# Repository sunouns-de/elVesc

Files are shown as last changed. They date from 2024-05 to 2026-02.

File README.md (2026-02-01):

# README

`Status: Completed (Archive State).`

This project is no longer being maintained as an active WIP. The primary reason is the availability of official VESC peripherals (such as the [VESC Dash 35B](https://www.vesclabs.com/product/vesc-dash-35b/) or the [VESC Rmcore](https://www.vesclabs.com/product/vesc-rmcore/)), which cover many of the original goals (CAN connectivity, LispBM scripting) natively and, in some aspects, more effectively.

**Important notes on the current state:**
1. **PCB Design:** The latest PCB design in this repository still contains errors. The board layout needs to be cross-checked against the schematics and revised before it can be considered fully functional.
2. **12V High-Side Switching:** Unlike many other solutions, including official ones like the RmCore, this design explicitly supports 12V high-side switching for vehicle lighting.
3. **Hardware Fixes:** The horn circuitry has already been corrected in the schematic but has not yet been implemented in the physical PCB layout.

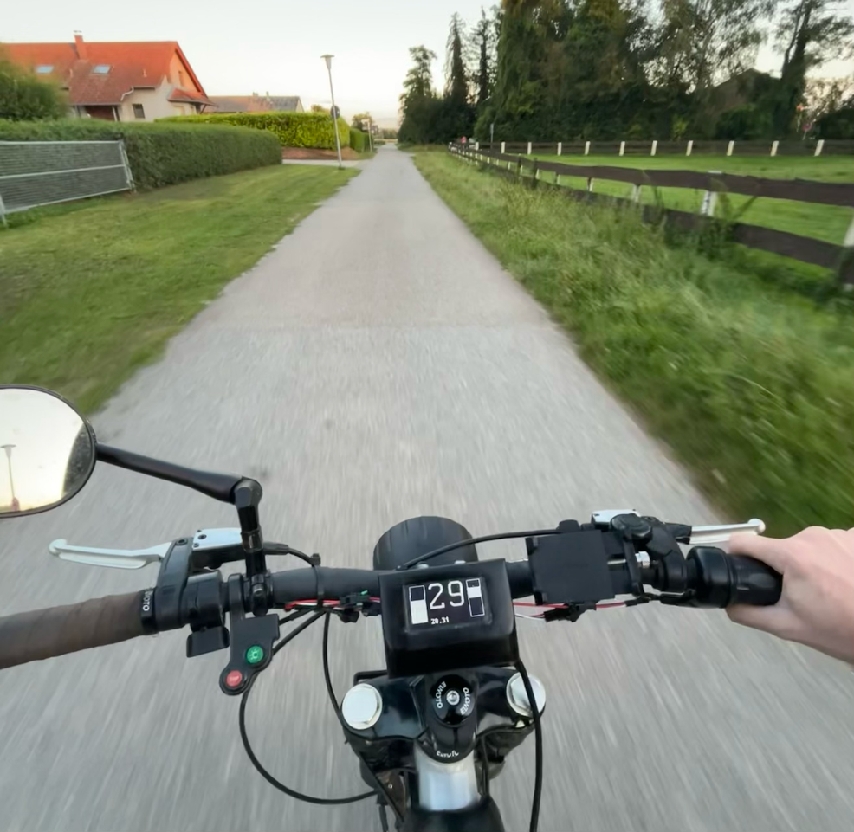
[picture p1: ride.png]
Summer 2024


## Overview

You find the code, flashable on an ESP32 DevKitC with PlatformIO in the submodule.

Everything needed for the PCB inside pcb-schematics.

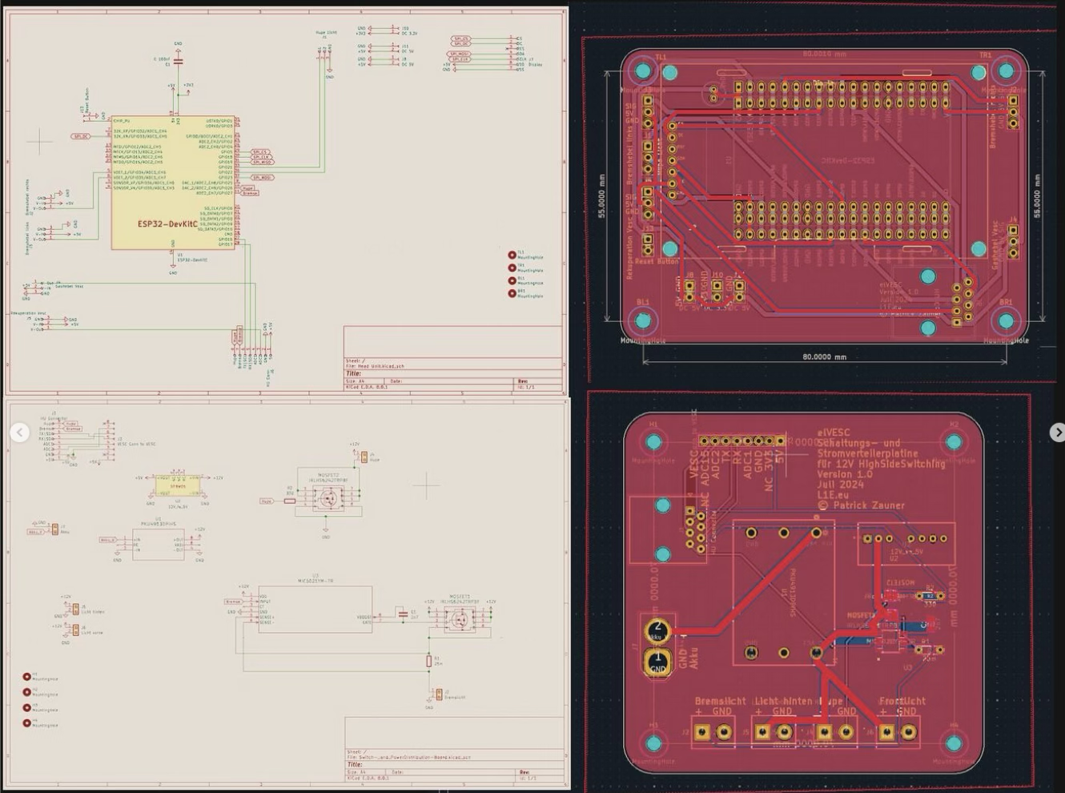
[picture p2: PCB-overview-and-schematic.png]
pcb-schematics


Link to Onshape Design of Headunit Mount in directory 3d design.
Other project designs will also be added here.

## Core concept

Replacement for original board electronics and an open platform to have a tachometer for any [VESC](https://vesc-project.com/) powered E-Bike.

### Headunit (Display)

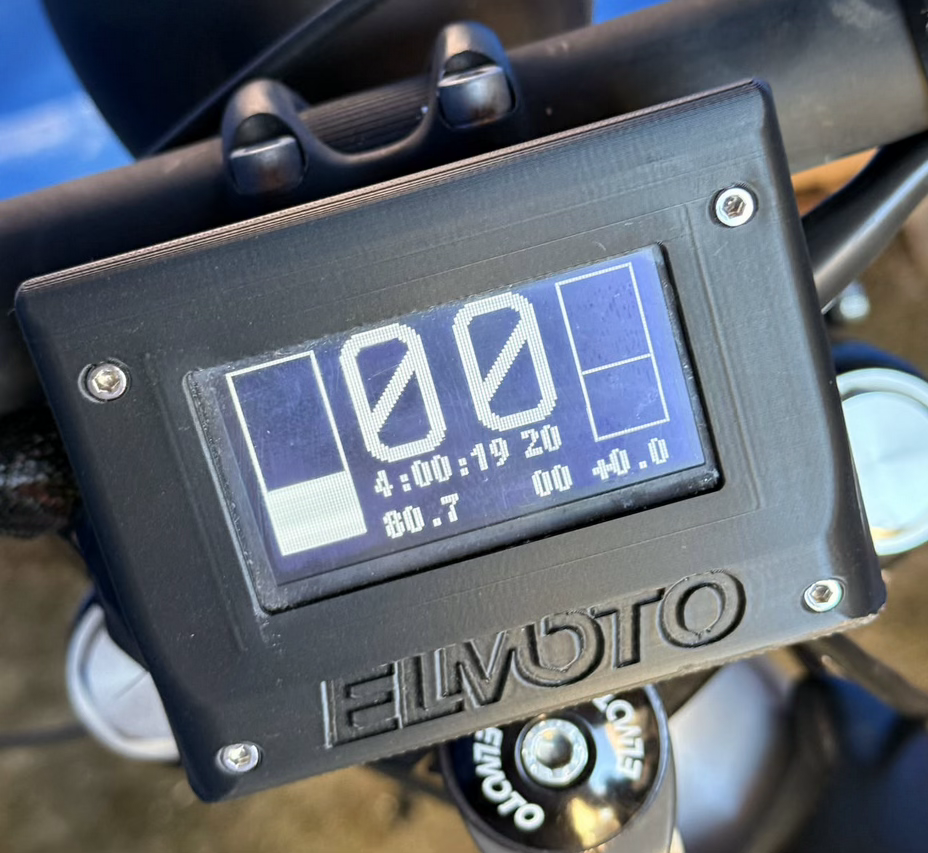
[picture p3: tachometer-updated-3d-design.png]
Tachometer in current housing


#### Implemented and working
Currently working on Tachometer:
- Speed
- Trip Kilometer (resets every power cycle)
- Time since Startup
- Average Speed
- Battery Voltage (mapped to left bar)
- Motor Current (mapped to right bar)
- Motor Power in kW (below right bar)
- Brake Lights
 - triggered when pulling any brake lever
 - also triggered when using regenerative braking above a configurable motor current

Currently all values (wheel diameter, battery voltage, max current, etc.) are hard coded.

Proper way for multiple bikes will be to utilize config files.

#### Implemented but not working
- Average Wh per km consumption
- Horn (probably hardware issue due to bad soldering)

#### Planned
- Odometer (saving distance to ESP32 flash)
- Don't try to calculate values like average speed or  but just get them from VESC

##### Ideas
- Smaller headunit but with more features: Utilizing also an ESP 32 C6 with Zigbee
 - Home Assistant integration
- OTA Updates
- Blinkers but requires more Pins on ESP32 or multiplexing
  - Also requires more than current 8 wires by using a normal RJ45-connector and Ethernet-cable to bottom or serial communication and therefore another microcontroller on the SPDB.

### Switching and Power Distribution Board (SPDB)

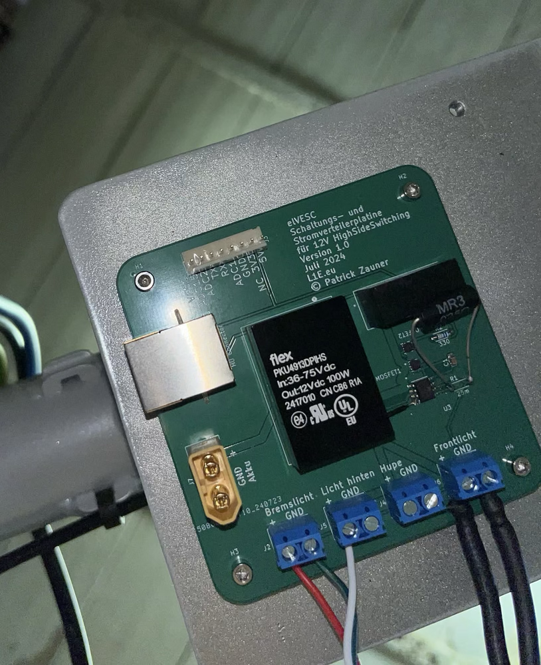
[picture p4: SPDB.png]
Switching and Power Distribution


Converts high battery voltage to 12V for the headlights and other components. (DC
/DC converter is not cheap, but great quality and has pleanty of headroom)

Also provides 5V for the Headunit: ESP32, Hall-Effect-Brake-Levers and Display. (ESP32 runs on 3V but the dev kit converts the incoming 5V to the usable 3V)

Connects the VESC to the rest of the system.

Turns on Brakelights and also provides power for the 12V lights.

#### Planned
- components with bigger footprints for easier soldering
 - MOSFETs
 - capacitors
 - resistors

#### Ideas

- USB-C in port and DC/DC converter for charging big E-Bike battery (not _really_ practical but I really want this hehe)
- USB-C out port for charging other devices or at least another 12V out to use existing products for this
- Eventually blinkers (my L1E-class-bike came without them from the manufacturer so they are not mandatory)

In combination with Headunit: Serial connection / CAN-BUS based system.

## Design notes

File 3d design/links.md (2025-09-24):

[Display Mount (Govecs has rights of logo)](https://cad.onshape.com/documents/d2e54b8ad2f1a2405cf1981f/w/7cc03ec50020e00fa81f538a/e/62ff2c873d72c78bf2272509)

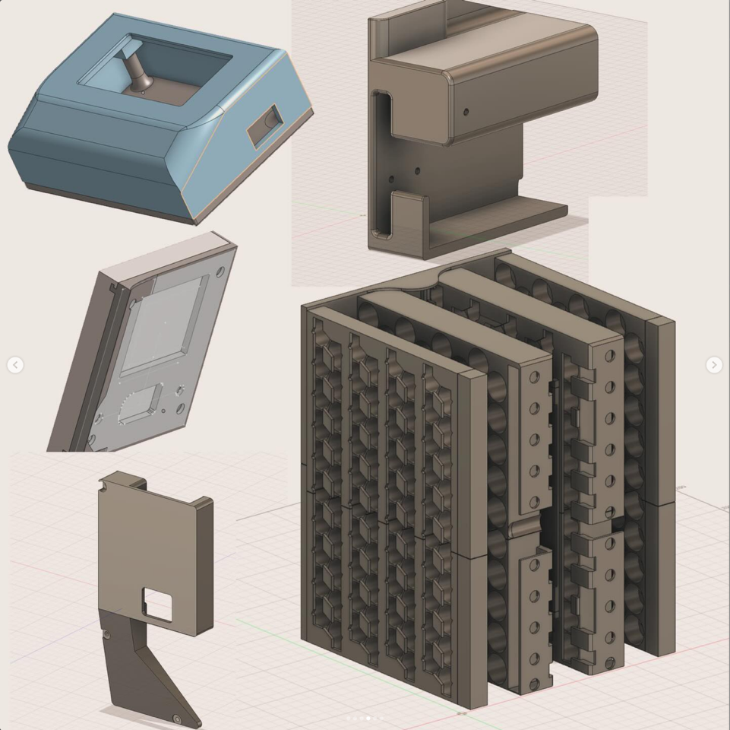
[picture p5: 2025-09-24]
3d-models-overview.png

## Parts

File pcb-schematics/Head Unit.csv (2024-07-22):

Id | Designator | Footprint | Quantity | Designation | Supplier and ref
1 | J10 | PinHeader_1x02_P2.54mm_Vertical | 1 | DC 3.3V
2 | J5 | PinHeader_1x03_P2.54mm_Vertical | 1 | Rekuperation Vesc
3 | J4 | PinHeader_1x03_P2.54mm_Vertical | 1 | Gashebel Vesc
4 | J7 | DIYMORE.CC | 1 | Display
5 | J8,J11 | PinHeader_1x02_P2.54mm_Vertical | 2 | DC 5V
6 | J3 | PinHeader_1x03_P2.54mm_Vertical | 1 | Bremshebel links
7 | J1 | PinHeader_1x03_P2.54mm_Vertical | 1 | Hupe Licht
8 | J2 | PinHeader_1x03_P2.54mm_Vertical | 1 | Bremshebel rechts
9 | J13 | PinHeader_1x02_P2.54mm_Vertical | 1 | Reset Button
10 | J6 | RJ45_Amphenol_54602-x08_Horizontal | 1 | HU Conn
11 | C1 | C_Radial_D5.0mm_H5.0mm_P2.00mm | 1 | C 100nF
12 | U1 | ESP32-DevKitC | 1 | ESP32-DevKitC

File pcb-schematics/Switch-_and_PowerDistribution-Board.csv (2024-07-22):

Id | Designator | Footprint | Quantity | Designation | Supplier and ref
1 | U2 | DPBW06_MWU | 1 | 12V_to_5V
2 | J2 | TerminalBlock_bornier-2_P5.08mm | 1 | Bremslicht
3 | R2 | R_Axial_DIN0204_L3.6mm_D1.6mm_P5.08mm_Horizontal | 1 | 330
4 | J3 | PinHeader_1x08_P2.54mm_Vertical | 1 | VESC Conn to VESC
5 | U1 | PKU4913DPIHS_FPM | 1 | PKU4913DPIHS
6 | J6 | TerminalBlock_bornier-2_P5.08mm | 1 | Licht vorne
7 | C1 | C_Radial_D5.0mm_H5.0mm_P2.00mm | 1 | 2n7
8 | J1 | RJ45_Amphenol_54602-x08_Horizontal | 1 | HU Connector
9 | MOSFET1,MOSFET2 | PQFN6_2X2_INF | 2 | IRLHS6242TRPBF
10 | J7 | AMASS_XT60-F_1x02_P7.20mm_Vertical | 1 | Akku
11 | R1 | R_Axial_DIN0204_L3.6mm_D1.6mm_P5.08mm_Horizontal | 1 | 25m
12 | U3 | SOIC-8_M_MCH | 1 | MIC5021YM-TR
13 | J5 | TerminalBlock_bornier-2_P5.08mm | 1 | Licht hinten
14 | J4 | TerminalBlock_bornier-2_P5.08mm | 1 | Hupe

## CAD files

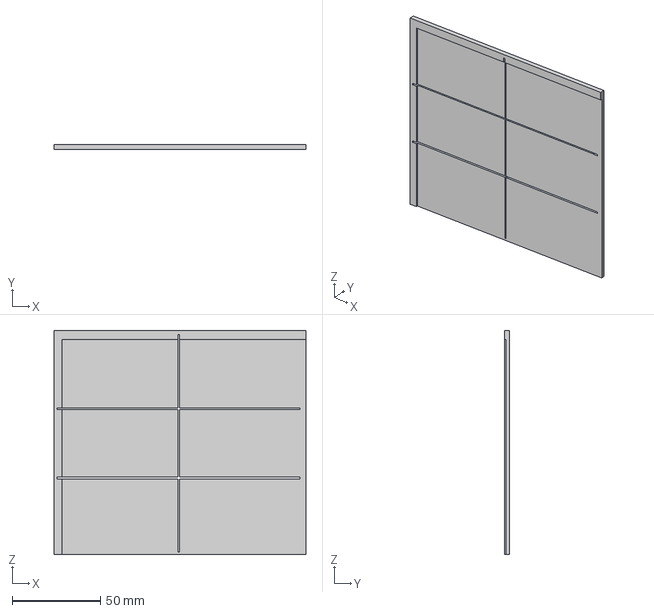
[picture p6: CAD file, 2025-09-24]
3d design/Schablone.3mf
142.7 x 3.00 x 126.9 mm

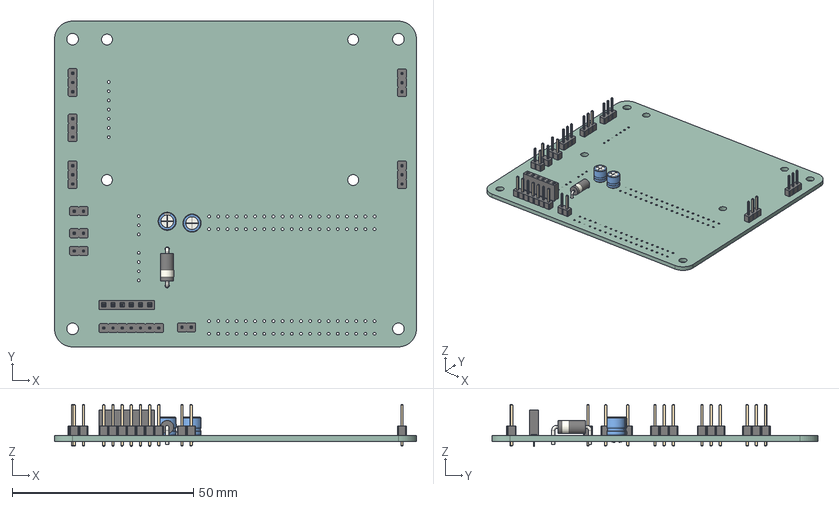
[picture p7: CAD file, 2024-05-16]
pcb-schematics/Head Unit/Head Unit.step
100.0 x 90.0 x 11.6 mm
CP_Radial_D50mm_P200mm
PinHeader_1x02_P254mm_Vertical x 4
C_Radial_D50mm_H50mm_P200mm
PinHeader_1x03_P254mm_Vertical x 5
D_DO-15_P10.16mm_Horizontal
PinHeader_1x07_P254mm_Vertical
PinSocket_1x06_P254mm_Vertical
Head Unit_PCB

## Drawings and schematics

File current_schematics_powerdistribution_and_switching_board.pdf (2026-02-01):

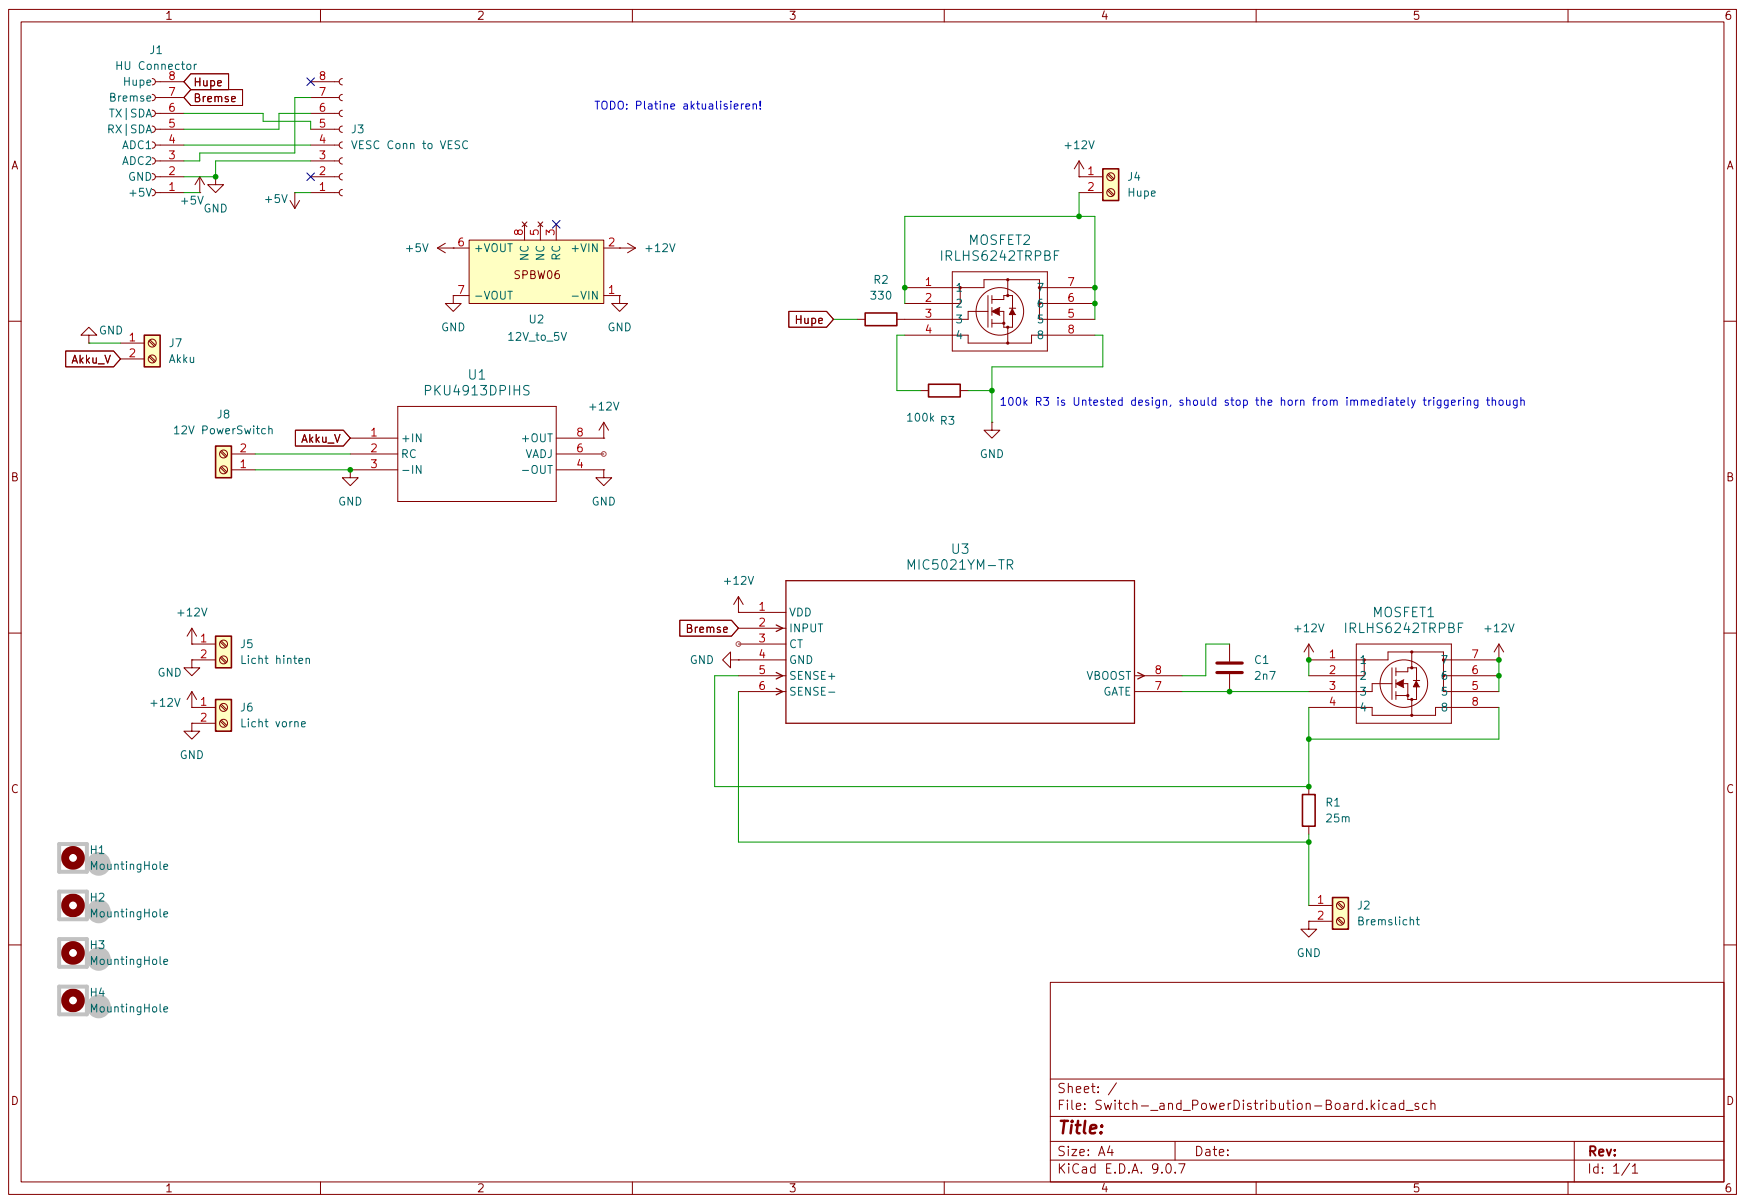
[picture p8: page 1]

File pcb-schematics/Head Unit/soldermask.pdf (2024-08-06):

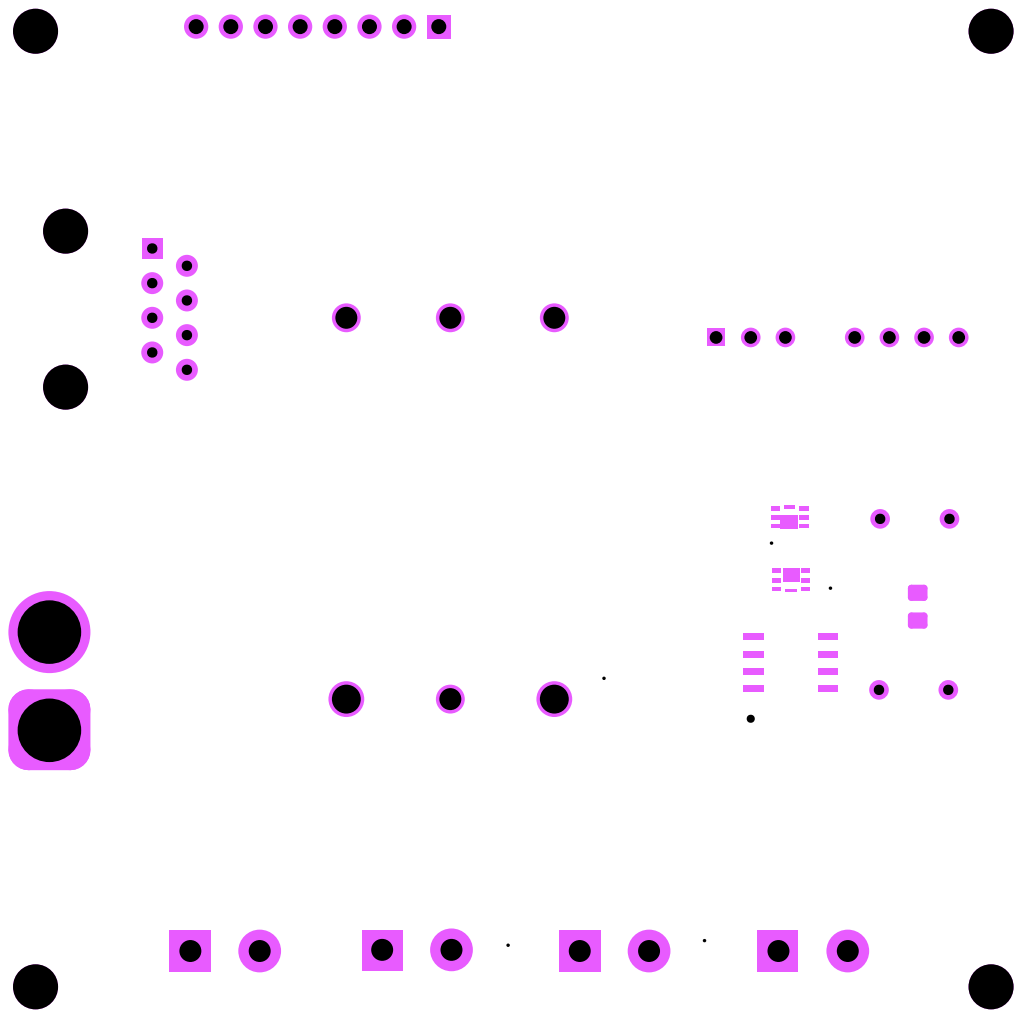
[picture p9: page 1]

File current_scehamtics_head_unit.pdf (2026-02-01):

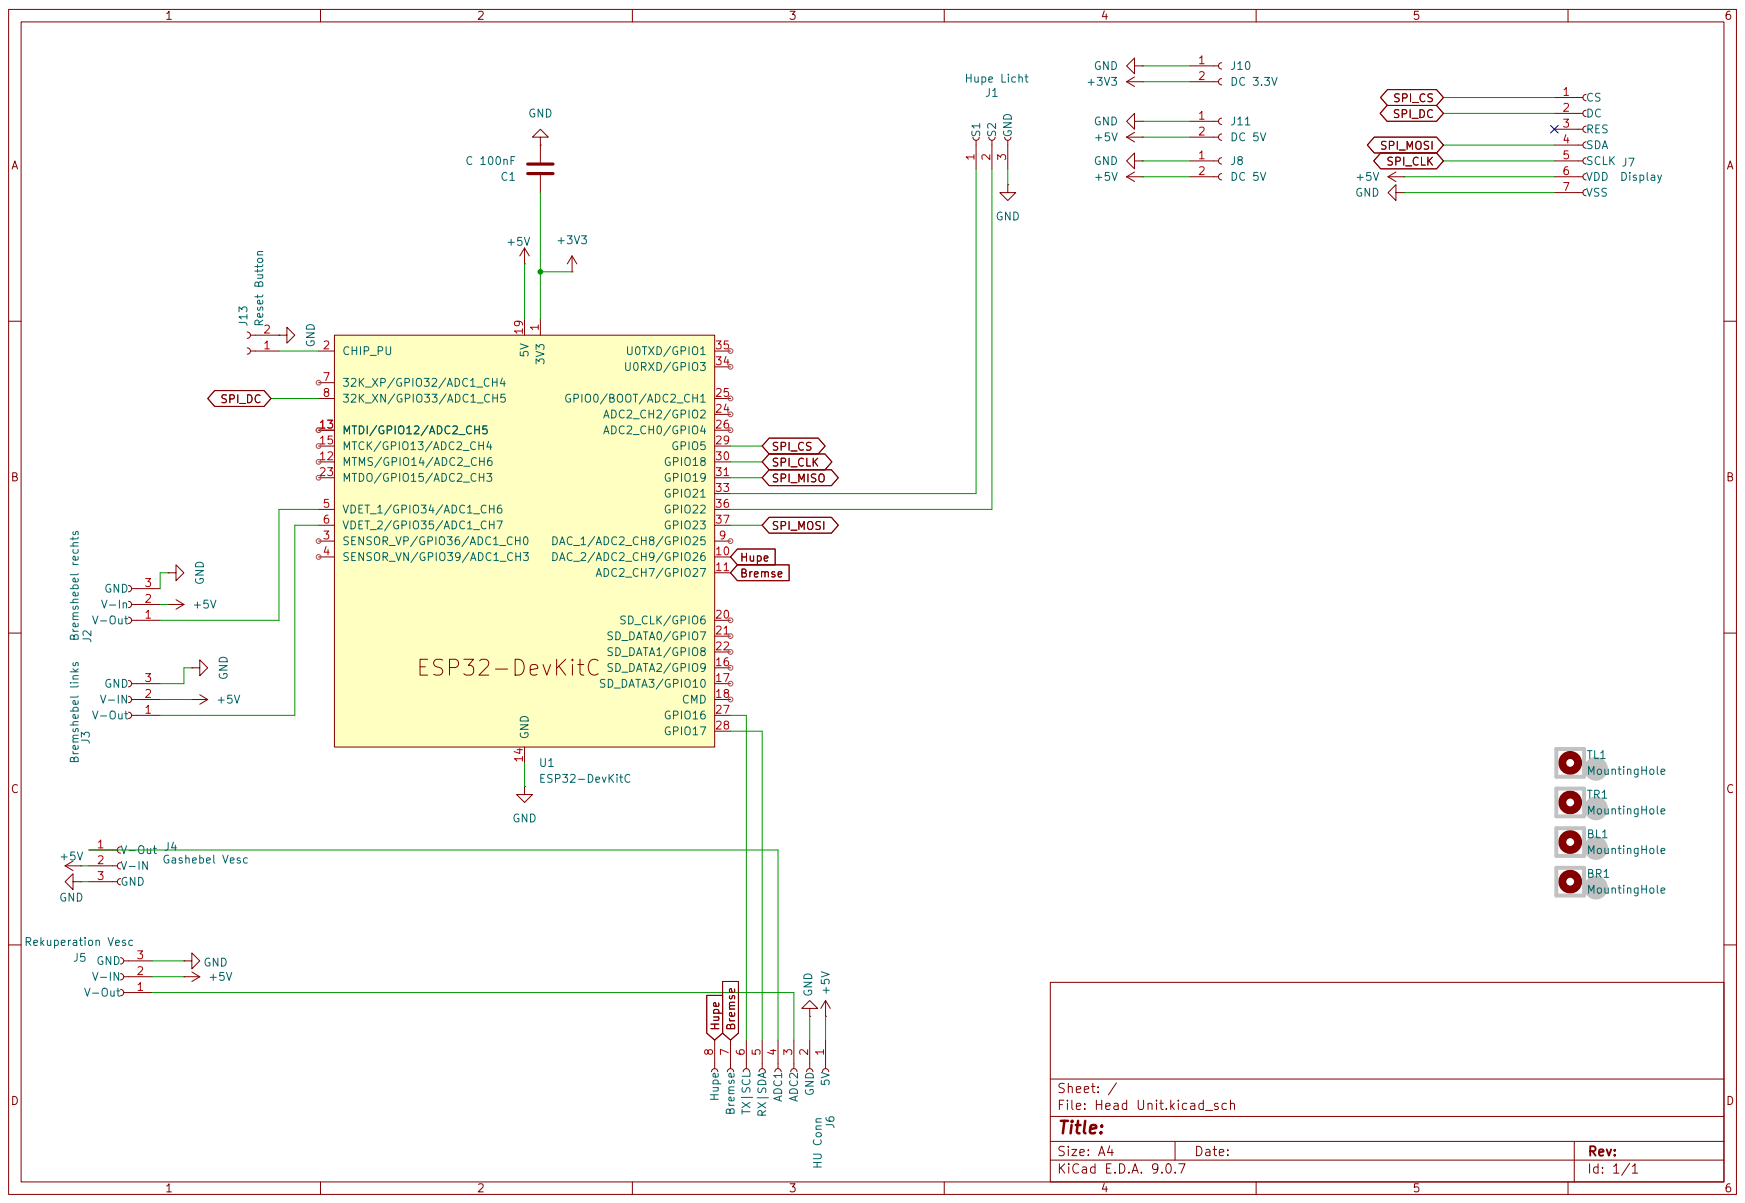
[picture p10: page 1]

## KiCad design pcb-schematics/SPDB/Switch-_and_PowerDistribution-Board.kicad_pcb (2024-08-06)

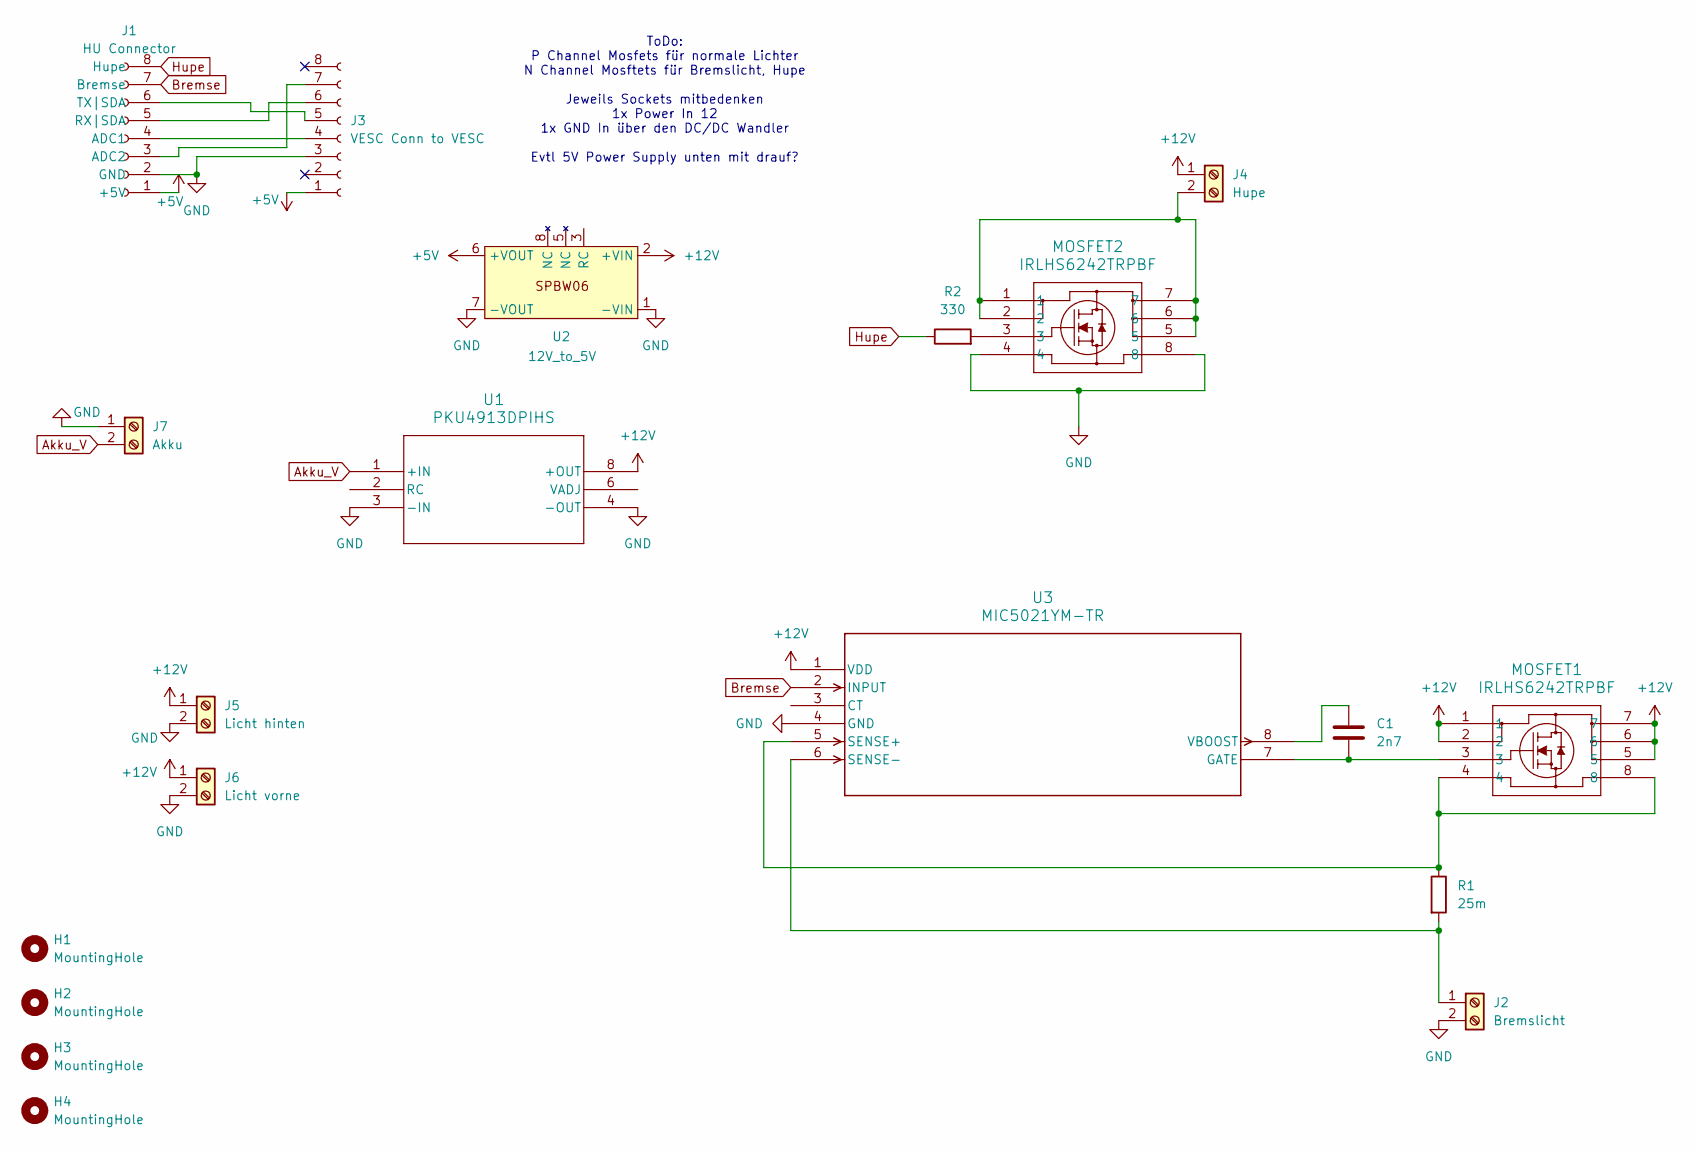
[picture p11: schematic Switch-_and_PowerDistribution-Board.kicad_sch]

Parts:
C1: 2n7; C_0805_2012Metric_Pad1.18x1.45mm_HandSolder
H1, H2, H3, H4: MountingHole; MountingHole_3.2mm_M3
J1: HU Connector; RJ45_Amphenol_54602-x08_Horizontal
J2: Bremslicht; TerminalBlock_bornier-2_P5.08mm
J3: VESC Conn to VESC; PinHeader_1x08_P2.54mm_Vertical
J4: Hupe; TerminalBlock_bornier-2_P5.08mm
J5: Licht hinten; TerminalBlock_bornier-2_P5.08mm
J6: Licht vorne; TerminalBlock_bornier-2_P5.08mm
J7: Akku; AMASS_XT60-F_1x02_P7.20mm_Vertical
MOSFET1, MOSFET2: IRLHS6242TRPBF; PQFN6_2X2_INF
R1: 25m; R_Axial_DIN0204_L3.6mm_D1.6mm_P5.08mm_Horizontal
R2: 330; R_Axial_DIN0204_L3.6mm_D1.6mm_P5.08mm_Horizontal
U1: PKU4913DPIHS; PKU4913DPIHS_FPM
U2: 12V_to_5V; DPBW06_MWU
U3: MIC5021YM-TR; SOIC-8_M_MCH

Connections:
+5V: J1.1 (+5V), J3.1, U2.6 (+VOUT)
+12V: J4.1, J5.1, J6.1, MOSFET1.1, MOSFET1.2, MOSFET1.5, MOSFET1.6, MOSFET1.7, U1.8 (+OUT), U2.2 (+VIN), U3.1 (VDD)
Akku_V: J7.2, U1.1 (+IN)
Bremse: J1.7 (Bremse), U3.2 (INPUT)
GND: J1.2 (GND), J2.2, J3.3, J5.2, J6.2, J7.1, MOSFET2.4, MOSFET2.8, U1.3 (-IN), U1.4 (-OUT), U2.1 (-VIN), U2.7 (-VOUT), U3.4 (GND)
Hupe: J1.8 (Hupe), R2.1
unnamed: J1.4 (ADC1), J3.4
unnamed: J1.3 (ADC2), J3.7 (Pin_2)
unnamed: J1.5 (RX|SDA), J3.6 (Pin_3)
unnamed: J1.6 (TX|SDA), J3.5 (Pin_4)
unnamed: J2.1, R1.2, U3.6 (SENSE-)
unnamed: J4.2, MOSFET2.1, MOSFET2.2, MOSFET2.5, MOSFET2.6, MOSFET2.7
unnamed: MOSFET2.3, R2.2
unnamed: C1.2, MOSFET1.3, U3.7 (GATE)
unnamed: MOSFET1.4, MOSFET1.8, R1.1, U3.5 (SENSE+)
unnamed: C1.1, U3.8 (VBOOST)

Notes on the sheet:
ToDo: P Channel Mosfets für normale Lichter N Channel Mosftets für Bremslicht, Hupe Jeweils Sockets mitbedenken 1x Power In 12 1x GND In über den DC/DC Wandler Evtl 5V Power Supply unten mit drauf?

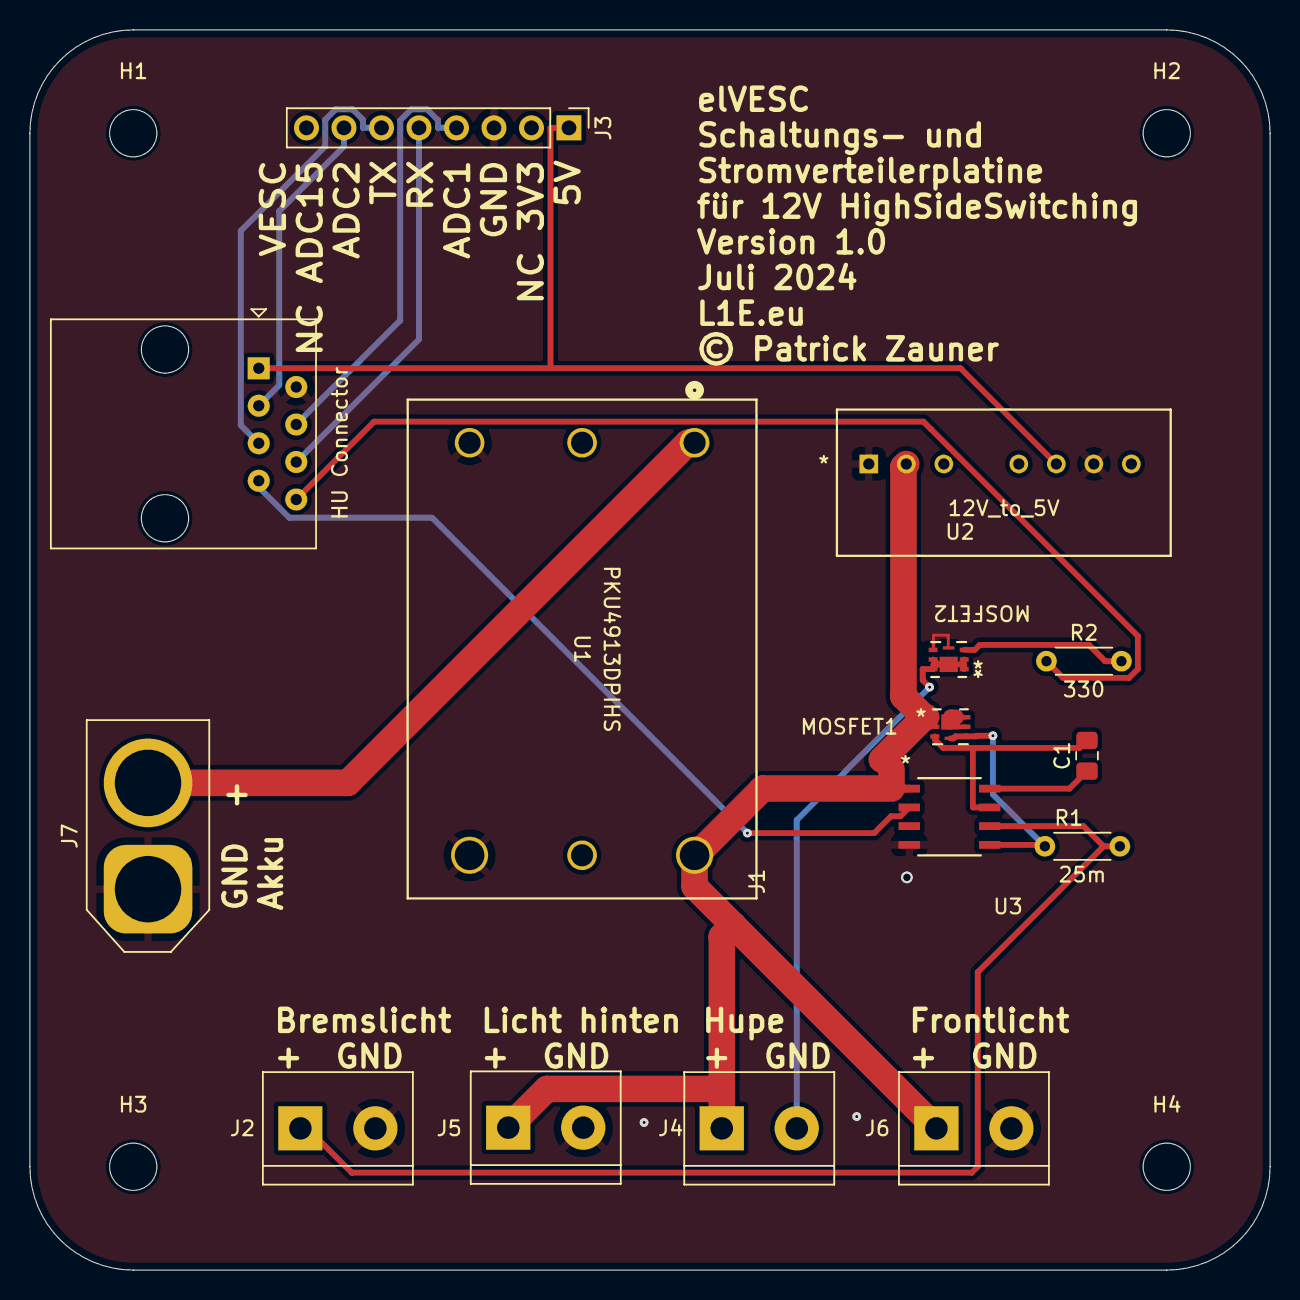
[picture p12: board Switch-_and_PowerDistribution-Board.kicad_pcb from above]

Board: 2 copper layers, 84.0 x 84.0 mm, 19 parts (0 on the bottom side), 16 nets.

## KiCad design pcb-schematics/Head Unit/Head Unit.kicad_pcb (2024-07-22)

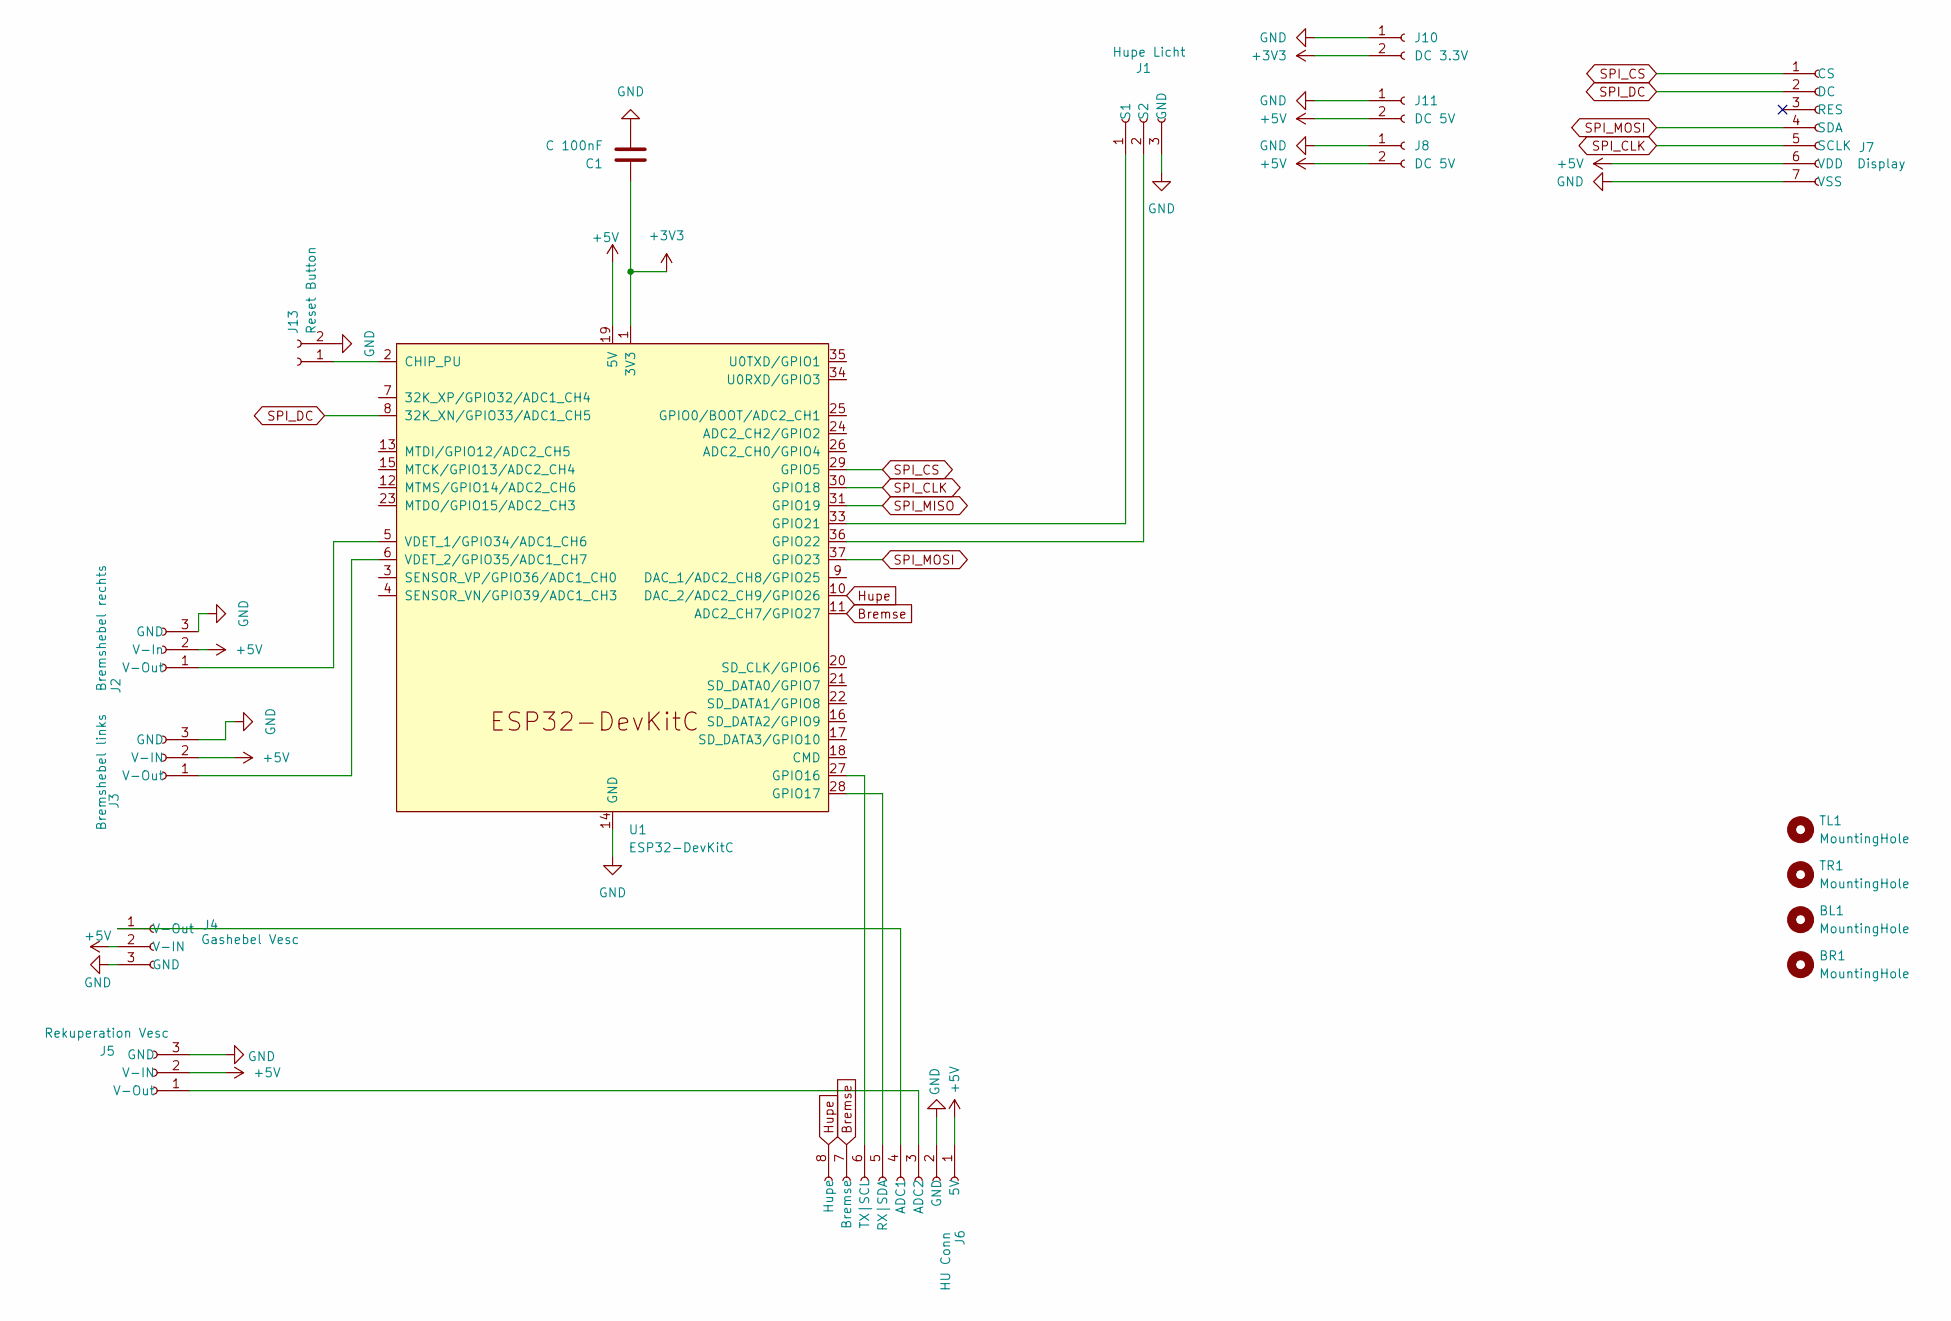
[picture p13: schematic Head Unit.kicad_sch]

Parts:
BL1: MountingHole; MountingHole_3.2mm_M3
BR1: MountingHole; MountingHole_3.2mm_M3
C1: C 100nF; C_Radial_D5.0mm_H5.0mm_P2.00mm
J1: Hupe Licht; PinHeader_1x03_P2.54mm_Vertical
J2: Bremshebel rechts; PinHeader_1x03_P2.54mm_Vertical
J3: Bremshebel links; PinHeader_1x03_P2.54mm_Vertical
J4: Gashebel Vesc; PinHeader_1x03_P2.54mm_Vertical
J5: Rekuperation Vesc; PinHeader_1x03_P2.54mm_Vertical
J6: HU Conn; RJ45_Amphenol_54602-x08_Horizontal
J7: Display; DIYMORE.CC
J8, J11: DC 5V; PinHeader_1x02_P2.54mm_Vertical
J10: DC 3.3V; PinHeader_1x02_P2.54mm_Vertical
J13: Reset Button; PinHeader_1x02_P2.54mm_Vertical
TL1: MountingHole; MountingHole_3.2mm_M3
TR1: MountingHole; MountingHole_3.2mm_M3
U1: ESP32-DevKitC

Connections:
+3V3: C1.1, J10.2, U1.1 (3V3)
+5V: J2.2 (V-In), J3.2 (V-IN), J4.2 (V-IN), J5.2 (V-IN), J6.1 (5V), J7.6 (VDD), J8.2, J11.2, U1.19 (5V)
Bremse: J6.7 (Bremse), U1.11 (ADC2_CH7/GPIO27)
GND: C1.2, J1.3 (GND), J2.3 (GND), J3.3 (GND), J4.3 (GND), J5.3 (GND), J6.2 (GND), J7.7 (VSS), J8.1, J10.1, J11.1, J13.2, U1.14 (GND), U1.32 (GND), U1.38 (GND)
Hupe: J6.8 (Hupe), U1.10 (DAC_2/ADC2_CH9/GPIO26)
unnamed: J1.1 (S1), U1.33 (GPIO21)
unnamed: J1.2 (S2), U1.36 (GPIO22)
unnamed: J2.1 (V-Out), U1.5 (VDET_1/GPIO34/ADC1_CH6)
unnamed: J3.1 (V-Out), U1.6 (VDET_2/GPIO35/ADC1_CH7)
unnamed: J4.1 (V-Out), J6.4 (ADC1)
unnamed: J5.1 (V-Out), J6.3 (ADC2)
unnamed: J6.5 (RX|SDA), U1.28 (GPIO17)
unnamed: J6.6 (TX|SCL), U1.27 (GPIO16)
unnamed: J13.1, U1.2 (CHIP_PU)
SPI_CLK: J7.5 (SCLK), U1.30 (GPIO18)
SPI_CS: J7.1 (CS), U1.29 (GPIO5)
SPI_DC: J7.2 (DC), U1.8 (32K_XN/GPIO33/ADC1_CH5)
SPI_MISO: U1.31 (GPIO19)
SPI_MOSI: J7.4 (SDA), U1.37 (GPIO23)

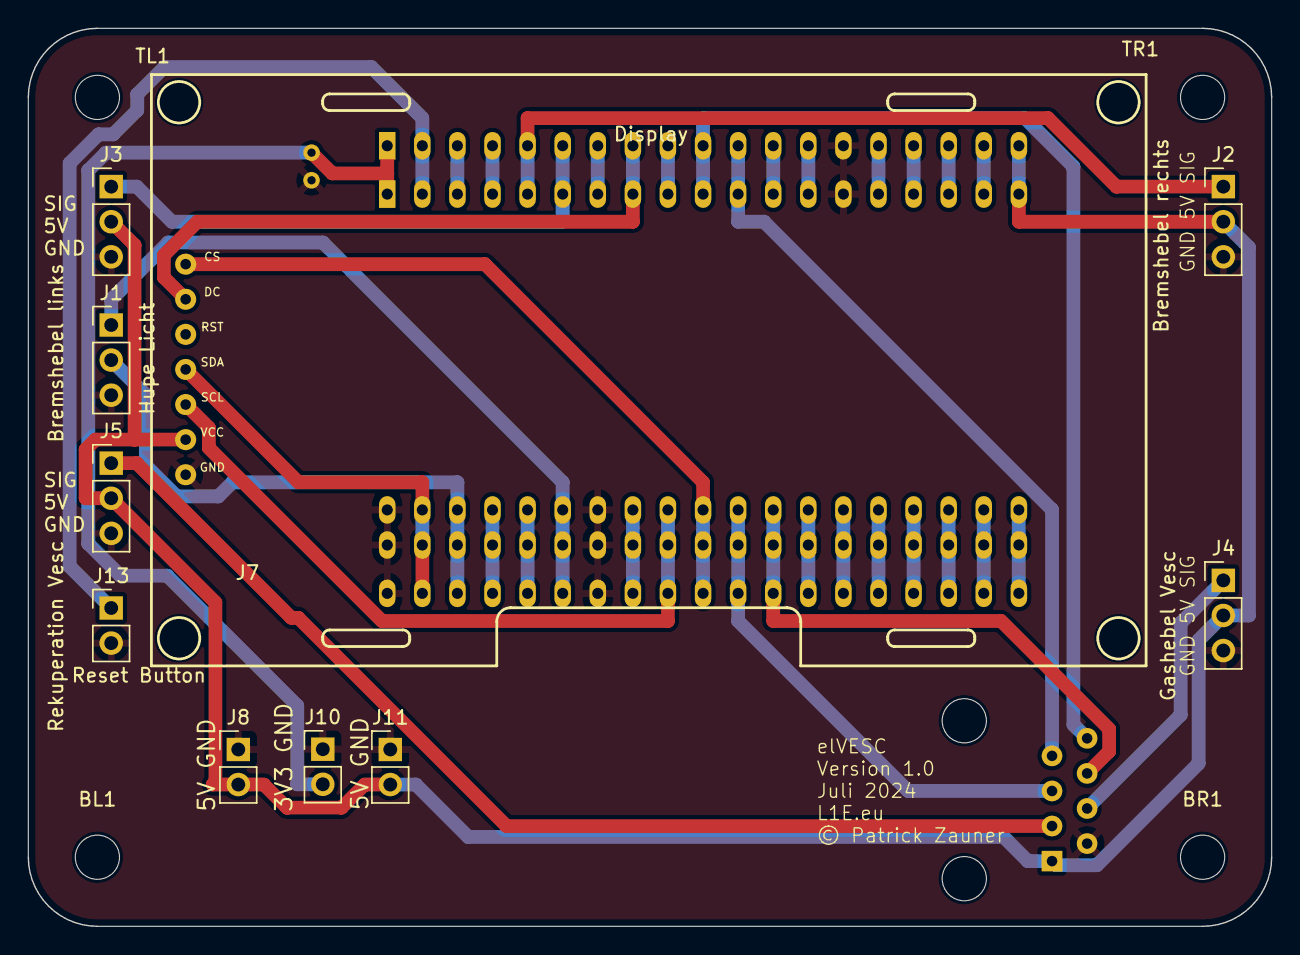
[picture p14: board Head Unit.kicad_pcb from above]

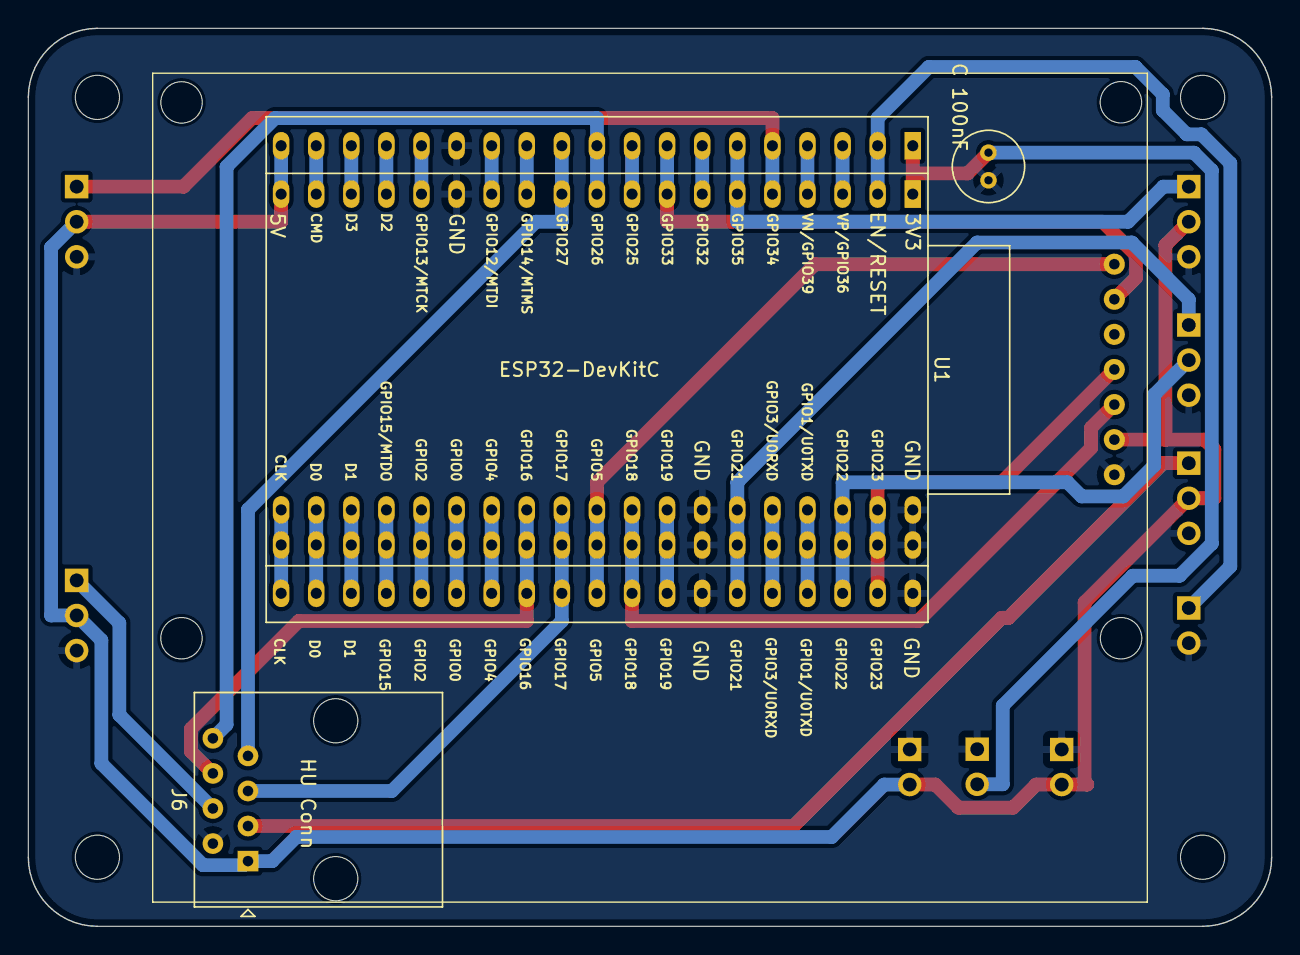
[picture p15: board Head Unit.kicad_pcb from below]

Board: 2 copper layers, 90.0 x 65.0 mm, 17 parts (3 on the bottom side), 18 nets.

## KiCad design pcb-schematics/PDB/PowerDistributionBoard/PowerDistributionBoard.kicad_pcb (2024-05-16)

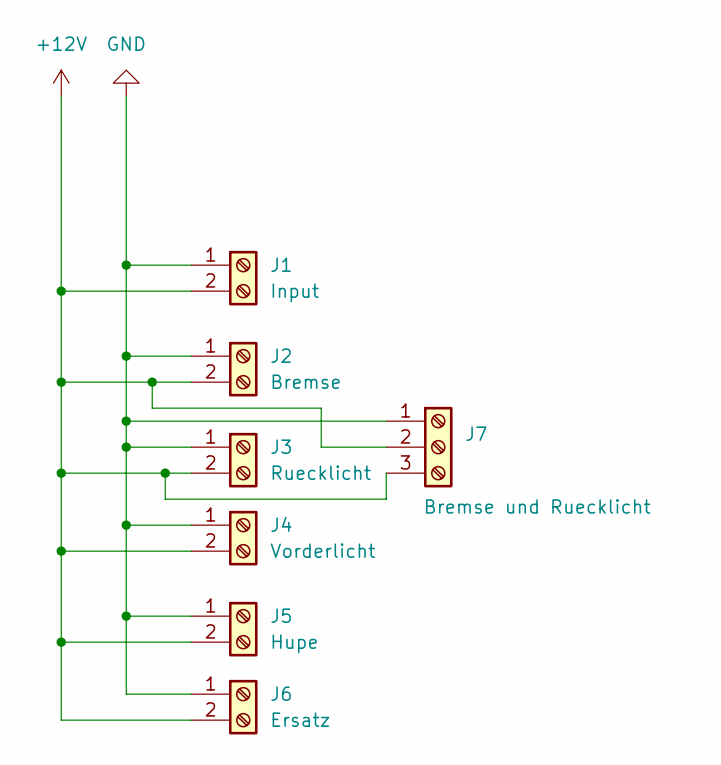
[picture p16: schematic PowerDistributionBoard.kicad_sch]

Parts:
J1: Input; TerminalBlock_bornier-2_P5.08mm
J2: Bremse; TerminalBlock_bornier-2_P5.08mm
J3: Ruecklicht; TerminalBlock_bornier-2_P5.08mm
J4: Vorderlicht; TerminalBlock_bornier-2_P5.08mm
J5: Hupe; TerminalBlock_bornier-2_P5.08mm
J6: Ersatz; TerminalBlock_bornier-2_P5.08mm
J7: Bremse und Ruecklicht; TerminalBlock_bornier-3_P5.08mm

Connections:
+12V: J1.2, J2.2, J3.2, J4.2, J5.2, J6.2, J7.2, J7.3
GND: J1.1, J2.1, J3.1, J4.1, J5.1, J6.1, J7.1

Board: 2 copper layers, 11 parts (0 on the bottom side), 2 nets, no tracks yet.

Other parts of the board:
BL: MountingHole_3.2mm_M3
BR: MountingHole_3.2mm_M3
TL: MountingHole_3.2mm_M3
TR: MountingHole_3.2mm_M3

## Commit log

2024-05-05 added esp32 code submodule
2024-05-16 schematics update
    [Head Unit-B_Cu.gbr, Head Unit-B_Mask.gbr, Head Unit-B_Silkscreen.gbr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]
2024-05-16 updated schematics
    [Head Unit.kicad_pcb, Head Unit.kicad_sch]
2024-05-16 3.3vdc to 5vdc converter
    [Head Unit.kicad_pcb, Head Unit.kicad_sch]
2024-05-17 rücklicht wiring
2024-05-18 before 5V change
    [Head Unit.kicad_pcb, Head Unit.kicad_sch]
2024-05-18 all hail 5V
    [Head Unit.kicad_sch]
2024-05-30 PCB Update to 2x RJ45
    [Head Unit.kicad_pcb, Head Unit.kicad_sch]
2024-07-22 updated schematics, now with a design change: only 1 cable between both; resulting in always on light, updated to RJ45-Connector, so easy to plug in and standardized cables available. battery to 12v 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
    everything coming with smaller footprints. great update.
    [Head Unit-B_Cu.gbr, Head Unit-B_Mask.gbr, Head Unit-B_Silkscreen.gbr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]
2025-09-24 added PCB overview image
2026-02-01 updated schematics, readme and added schematics as pdf files
    [Switch-_and_PowerDistribution-Board.kicad_sch]

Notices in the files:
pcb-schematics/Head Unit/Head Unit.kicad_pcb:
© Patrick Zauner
